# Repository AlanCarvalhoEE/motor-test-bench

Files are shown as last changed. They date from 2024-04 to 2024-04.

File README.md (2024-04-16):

# Motor Test Bench

This project consists of a test bench for small DC motors. The main objective of the system is to enable the characterization of motors with unknown data. The system performs measurements of rotational speed and torque of the motor under test while gradually varying the load on the motor shaft.

The speed is measured using a quadrature encoder. The encoder disc is coupled to the motor shaft and as it rotates, it generates pulses in an optical switch. Counting these pulses, when related to elapsed time, allows for the calculation of the rotational speed of the shaft.

The torque is indirectly measured. A lever arm is pressed against the motor shaft by a spring, whose tension can be varied, thereby altering the load on the shaft. The rotation of the motor shaft causes this lever arm to press against a load cell, which measures the applied force. By relating the measured force to the length of the lever arm, the torque is calculated.

During a test, the load on the motor shaft is gradually increased automatically. A stepper motor provides linear advancement under the spring, increasing its tension and consequently the load.

With the obtained data, it is possible to generate "torque vs. speed" and "power vs. speed" graphs of the motor, as well as identify parameters such as maximum speed, holding torque, and maximum power.

The current version of the project is still a prototype. In the next version, all electronics will be integrated, and new functionalities will be developed. The system will include measurement of the motor's input current, allowing for the calculation of its input power and consequently, its efficiency.

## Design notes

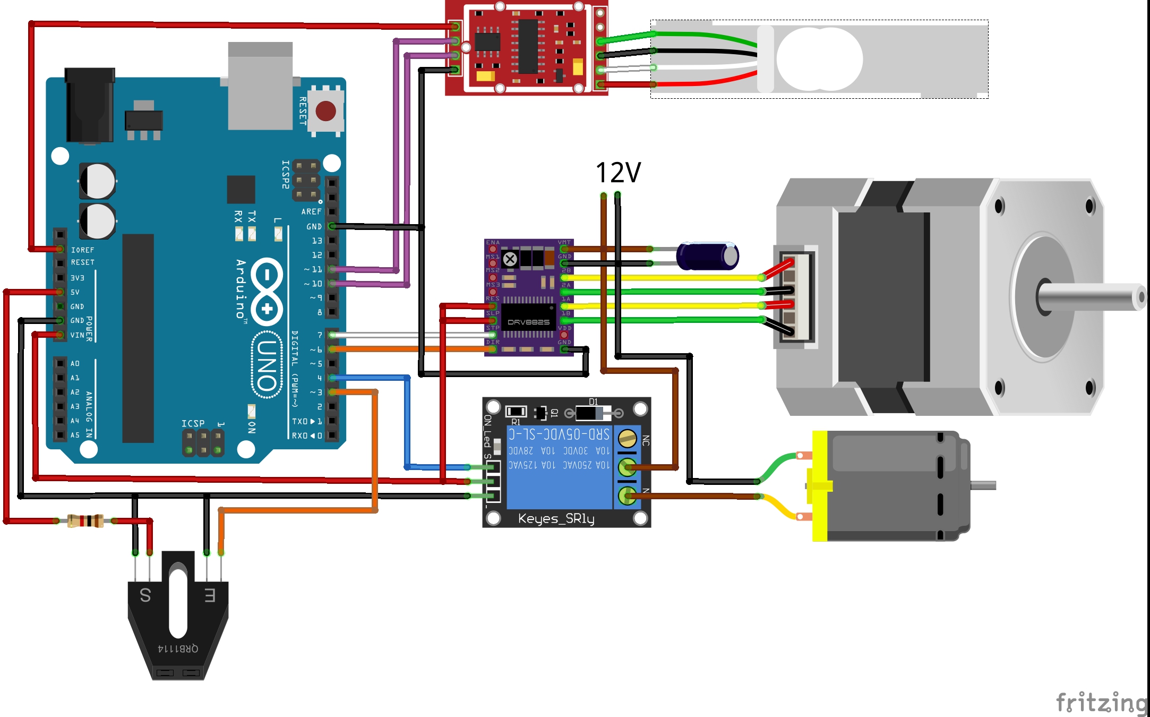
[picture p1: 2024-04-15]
Electronics/Electronics schematic.jpg

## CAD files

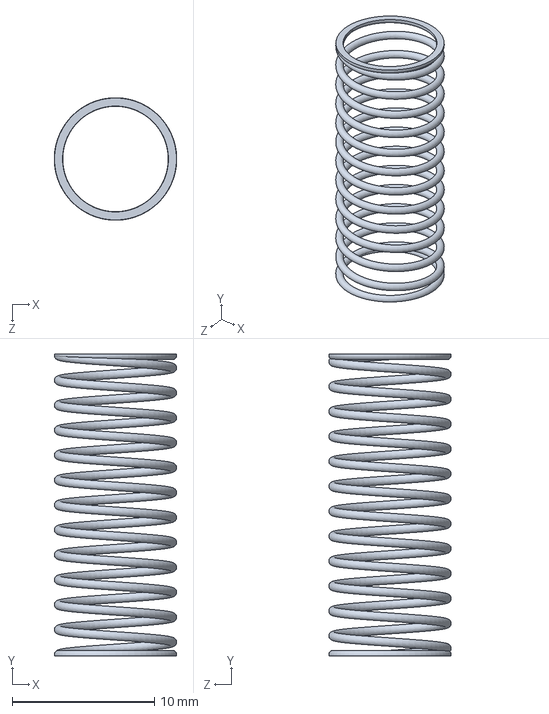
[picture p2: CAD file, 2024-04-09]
3D/Parts to buy/Spring 8x21.SLDPRT
8.60 x 21.2 x 8.60 mm

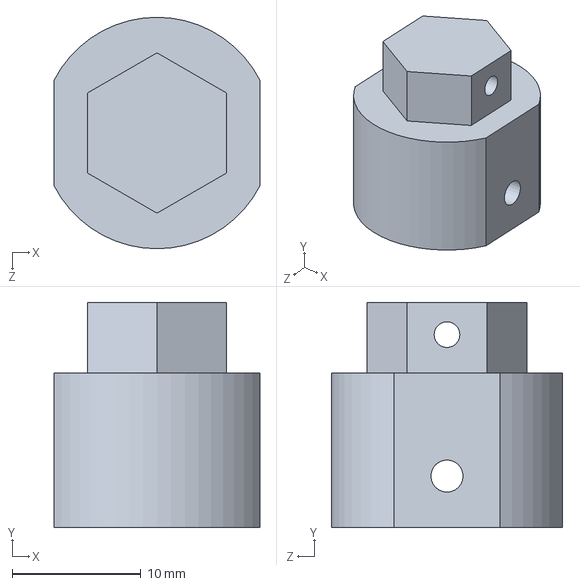
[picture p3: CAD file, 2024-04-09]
3D/Parts to manufacture/Stepper shaft adapter.SLDPRT
16.0 x 17.5 x 18.0 mm

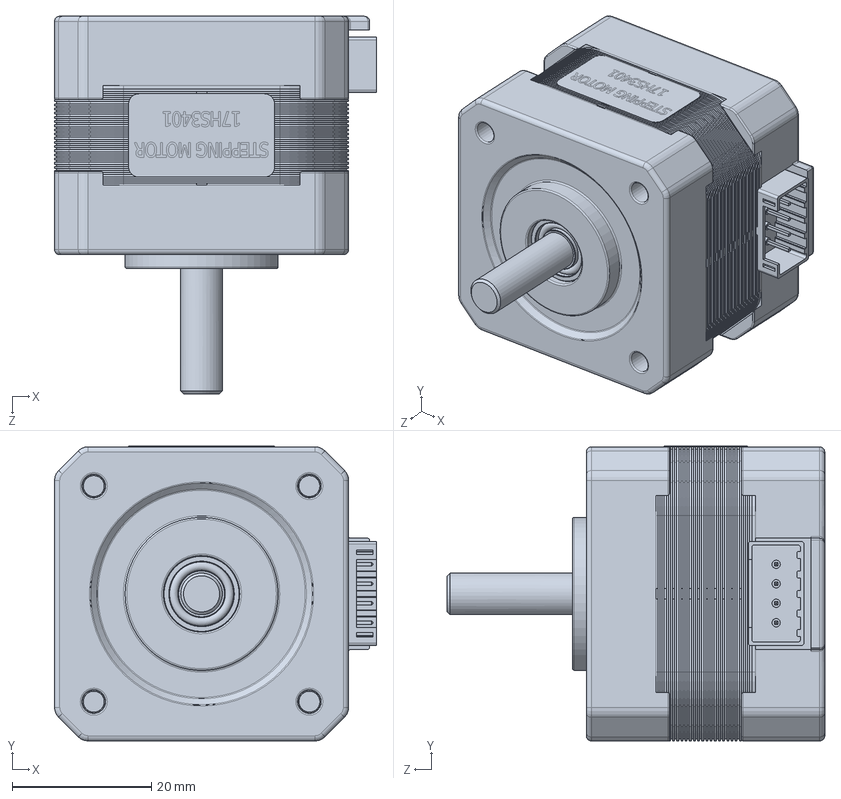
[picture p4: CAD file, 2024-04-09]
3D/Parts to buy/Stepper motor 17HS3401.SLDPRT
46.3 x 42.4 x 54.3 mm

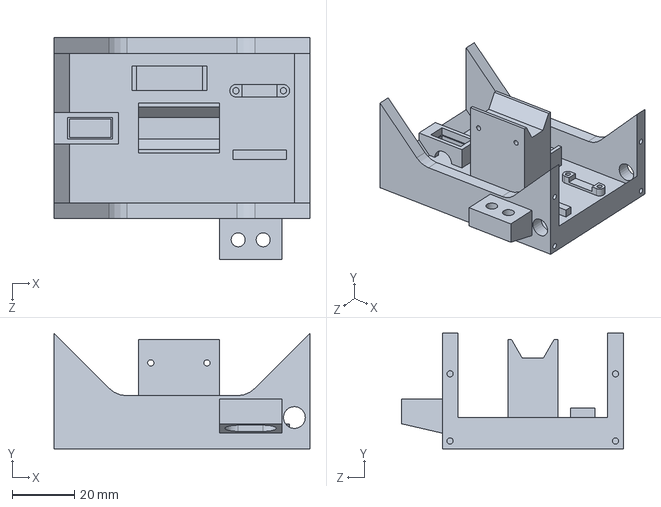
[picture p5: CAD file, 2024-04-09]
3D/Parts to manufacture/Base.SLDPRT
82.0 x 37.0 x 71.0 mm

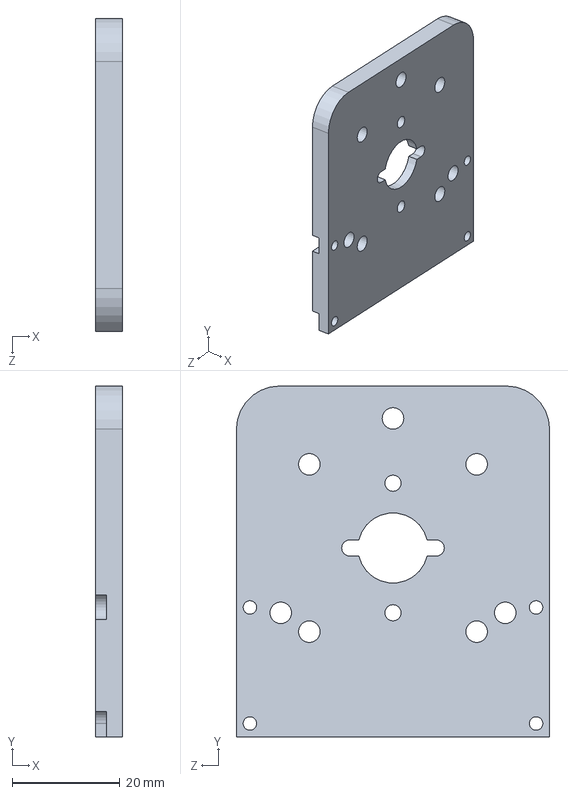
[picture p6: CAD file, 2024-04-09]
3D/Parts to manufacture/Test motor mount.SLDPRT
5.00 x 65.0 x 58.0 mm

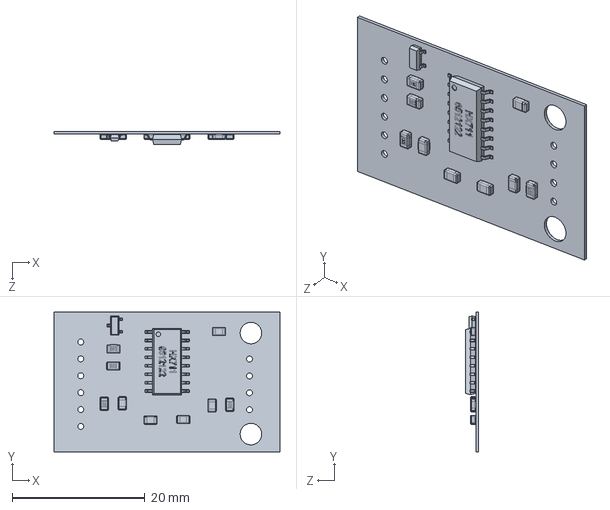
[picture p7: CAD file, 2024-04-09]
3D/Parts to buy/HX711 module.SLDPRT
34.0 x 21.0 x 1.97 mm

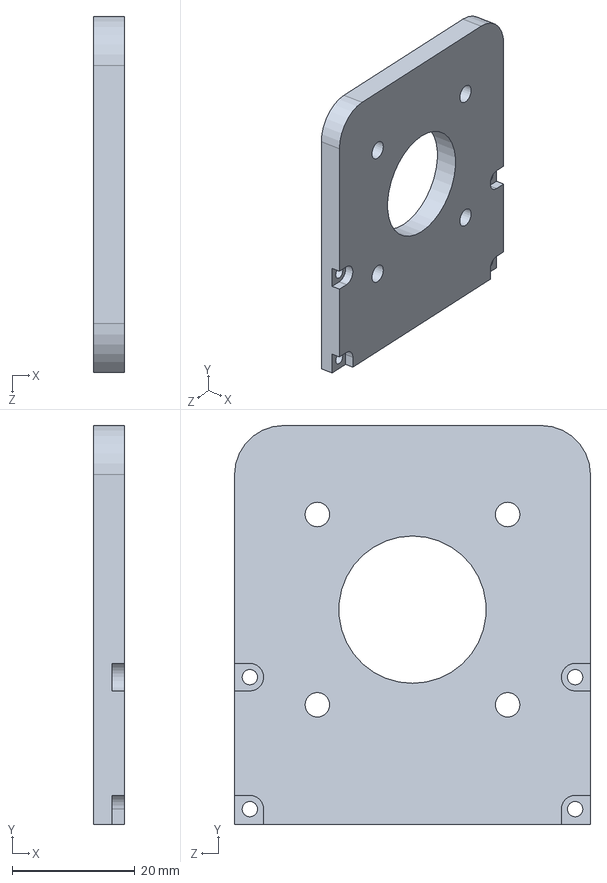
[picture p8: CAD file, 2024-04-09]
3D/Parts to manufacture/Stepper mount.SLDPRT
5.00 x 65.0 x 58.0 mm

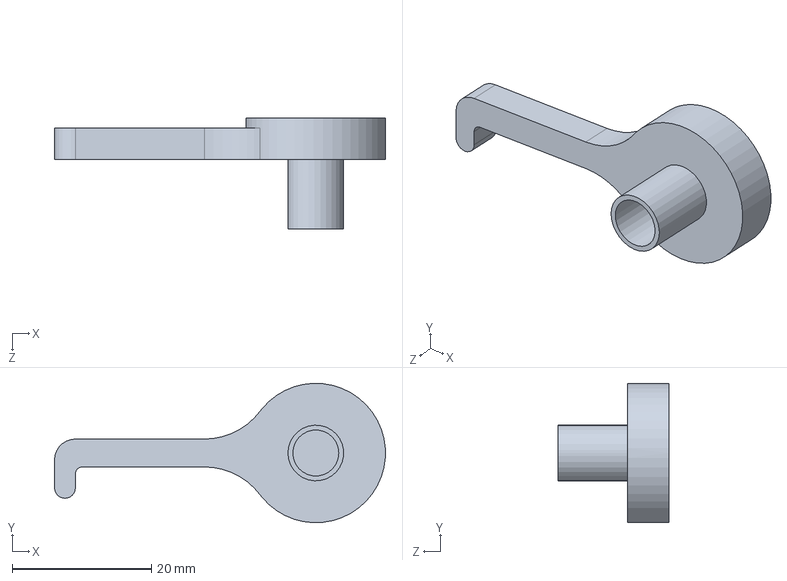
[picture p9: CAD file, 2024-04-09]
3D/Parts to manufacture/Lever arm.SLDPRT
47.5 x 20.0 x 16.0 mm

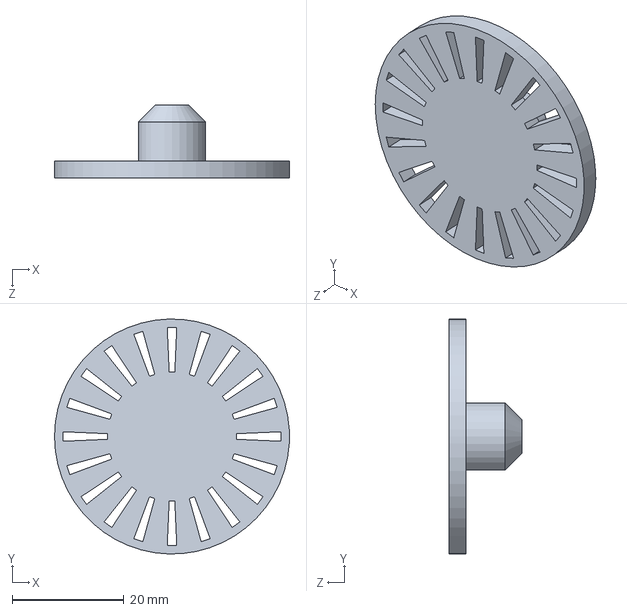
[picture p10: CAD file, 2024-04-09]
3D/Parts to manufacture/Encoder disk.SLDPRT
42.0 x 42.0 x 13.0 mm

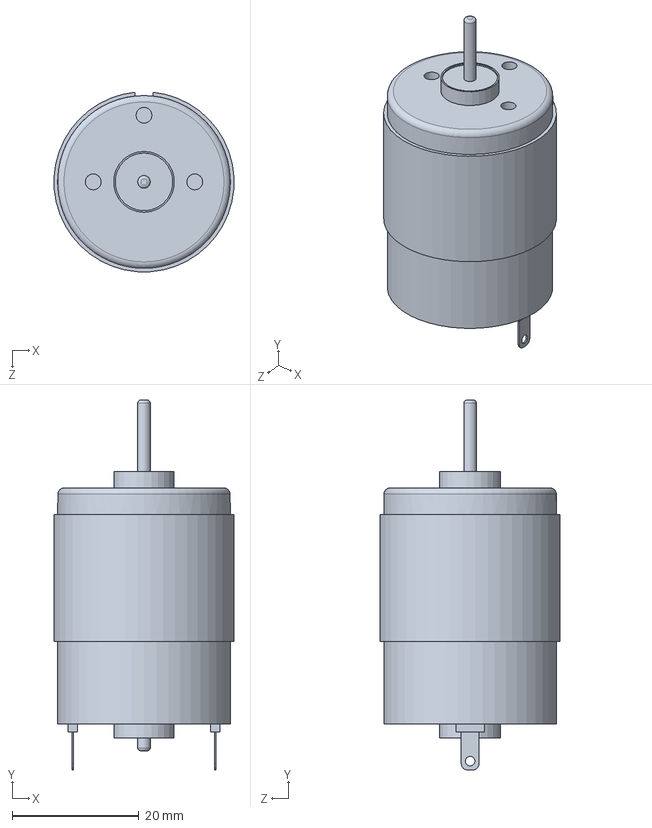
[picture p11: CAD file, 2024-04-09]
3D/Parts to buy/DC motor 27x37mm.SLDPRT
28.4 x 58.3 x 28.3 mm

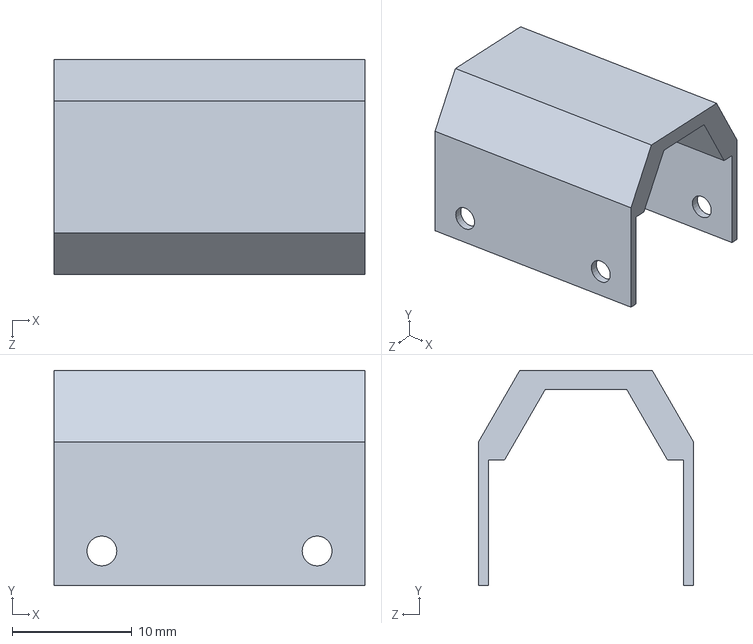
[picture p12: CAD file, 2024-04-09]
3D/Parts to manufacture/Spring cover.SLDPRT
26.0 x 18.0 x 18.0 mm

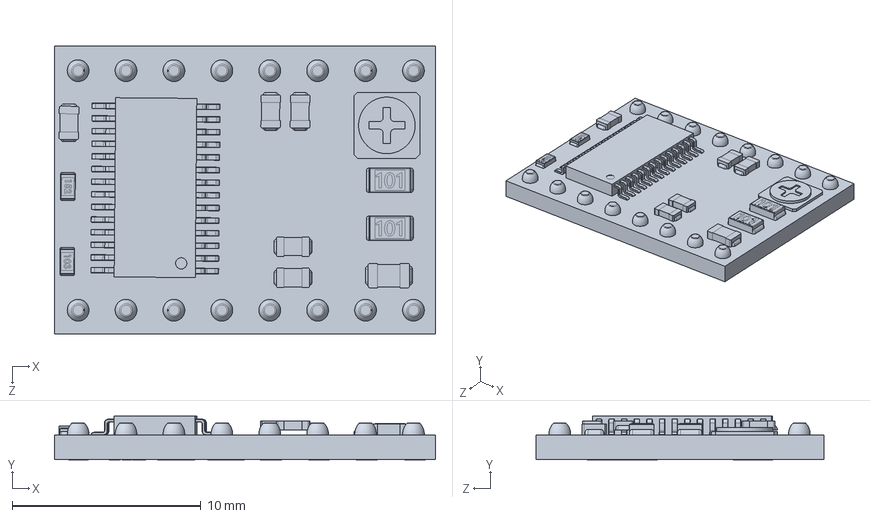
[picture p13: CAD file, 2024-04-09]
3D/Parts to buy/Stepper Motor Driver DRV8825.SLDPRT
20.2 x 2.31 x 15.2 mm

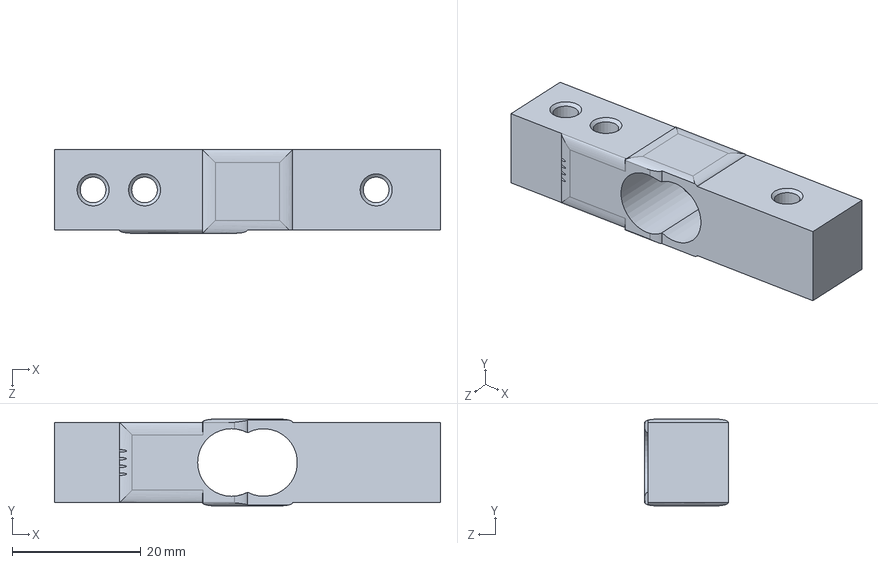
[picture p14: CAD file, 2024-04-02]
3D/Parts to buy/Load cell 5kg.SLDPRT
60.0 x 13.5 x 13.0 mm

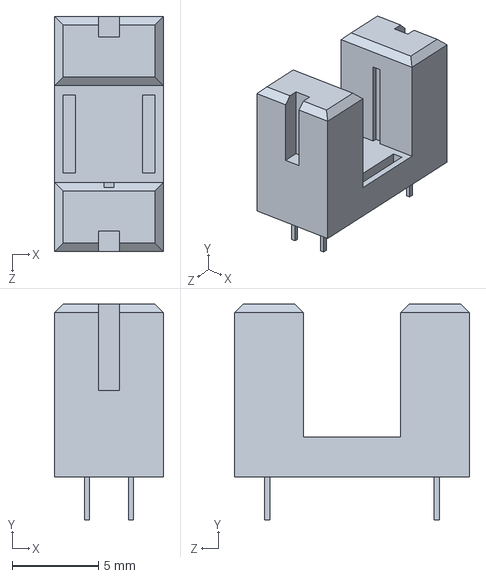
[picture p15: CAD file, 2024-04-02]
3D/Parts to buy/Optical Switch.SLDPRT
6.30 x 12.5 x 13.6 mm

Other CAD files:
3D/Bench assembly.SLDASM
3D/Parts to buy/Allen cilindrical head screw M4x10.SLDPRT
3D/Parts to buy/Hex screw M6x40.SLDPRT
3D/Parts to buy/Allen cilindrical head screw M3x8.SLDPRT
3D/Parts to buy/Allen button head screw M2,5x6.SLDPRT
3D/Parts to buy/Nut M6.SLDPRT
3D/Parts to buy/Phillips self-tapping pan head screw 2,2x6,5.SLDPRT
3D/Parts to manufacture/Screw adapter.SLDPRT

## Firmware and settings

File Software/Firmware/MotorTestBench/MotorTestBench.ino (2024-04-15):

// Motor Test Bench V1.0
// Developer: Alan Carvalho
// Date: 14/04/2024

#include "AccelStepper.h"  // Library to control the stepper motor
#include "HX711.h"         // Library to control the HX711 module

// HX711 pins
#define LOADCELL_DT 10
#define LOADCELL_SCK 11

// Relay pin
#define RELAY_S 4

// Optical switch pin
#define OPTICAL_SWITCH 3

// Stepper driver pins
#define STEPPER_DIR 6
#define STEPPER_STEP 7

// Bench parameters
#define STEPPER_SPEED -100    // Stepper motor speed
#define ARM_LENGTH 0.035      // Lever arm length (m)
#define ENCODER_POINTS 20.0   // Number of windows in the encoder disk
#define MAX_PULSES 100        // Number of pulses to restart the counting

HX711 loadCell;                                                       // HX711 library object
AccelStepper stepper = AccelStepper(1, STEPPER_STEP, STEPPER_DIR);    // AccelStepper library object

bool running = false;                   // Indicates the test is running
float mass = 0;                         // Mass on the load cell (g)
float torque = 0;                       // Torque generated by the motor (mN.m)
float speed = 0;                        // Motor shaft speed (RPM)
volatile int pulseCount = 0;            // Encoder pulse count
unsigned long currentTime = 0;          // Current time on speed calculation (ms)
unsigned long initialTime = 0;          // Initial time on speed calculation (ms)
const long readingInterval = 100;        // Interval between readings (ms)
unsigned long lastReading = 0;          // Time of the last reading (ms)
const long maximumPulseInterval = 1000; // Maximum time between two encoder pulse to assume it is not running (ms)
unsigned long lastPulseTime = 0;        // Time when the last encoder pulse happened (ms)
const long testFinishInterval = 3000;   // Interval to stop the test after the motor speed gets to zero (ms)
unsigned long zeroSpeedTime = 0;        // Time when the motor speed gets to zero (ms)


void setup() 
{
  Serial.begin(115200);  // Open the serial port

  // Configure pins
  pinMode(OPTICAL_SWITCH, INPUT_PULLUP);
  pinMode(RELAY_S, OUTPUT);

  // Configure the HX711 sensor
  loadCell.begin(LOADCELL_DT, LOADCELL_SCK);
  loadCell.set_scale(440);
  loadCell.tare();

  // Configure the interrupt to detect encoder pulses
  attachInterrupt(digitalPinToInterrupt(OPTICAL_SWITCH), countPulse, RISING);

  // Start with the motor turned off
  digitalWrite(RELAY_S, LOW);

  // Set stepper maximum speed
  stepper.setMaxSpeed(100);
}


void loop() 
{
  if (Serial.available() > 0) 
  {
    String command = Serial.readString();

    if (command.indexOf("START") > -1) startTest();
    else if (command.indexOf("STOP") > -1) stopTest(false);
  }

  if (running) 
  {
    stepper.runSpeed();

    if ((millis() - lastReading) > readingInterval) 
    {
      // Get all the necessary data
      getSpeed();
      getTorque();

      // Print the collected data on the serial port
      printData();

      lastReading = millis();
    }

    // Encoder is not moving
    if ((millis() - lastPulseTime) > maximumPulseInterval) pulseCount = 0;
  }
}


void getSpeed() 
{
  currentTime = millis() - initialTime;
  speed = 60000 * ((pulseCount / ENCODER_POINTS) / currentTime);
  if (speed < 0) speed = 0;

  if (pulseCount > MAX_PULSES) 
  {
    pulseCount = 0;
    initialTime = millis();
  }

  //if(speed == 0)
  //{
    //if(zeroSpeedTime == 0) zeroSpeedTime = millis();
    //else if ((millis() - zeroSpeedTime) > testFinishInterval) stopTest(true);
  //}
}

void getTorque() 
{
  mass = loadCell.get_units();
  torque = 9.81 * mass * ARM_LENGTH;
  if (torque < 0) torque = 0;
}

void countPulse() 
{
  pulseCount++;
  lastPulseTime = millis();
}

void printData() 
{
  Serial.print(speed);
  Serial.print("|");
  Serial.print(torque);
  Serial.println("");
}

void startTest()
{
  running = true;
  
  digitalWrite(RELAY_S, HIGH);
  
  Serial.println("MOTOR TEST STARTED");
  Serial.println("");
  Serial.println("Speed (RPM)|Torque (mN.m)");
     
  stepper.setSpeed(STEPPER_SPEED);
}

void stopTest(bool status)
{
  running = false;
  pulseCount = 0;
  zeroSpeedTime = 0;
  
  digitalWrite(RELAY_S, LOW);
  
  if (status) Serial.println("MOTOR TEST FINISHED");
  else Serial.println("MOTOR TEST STOPPED");
  Serial.println("");

  stepper.stop();
}

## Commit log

2024-04-01 3D models included
    [Current sensor module ACS712.SLDPRT, Encoder disk.SLDPRT, Encoder disk.STL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]
2024-04-02 3D models updated
    [Allen button head screw M2,5x6.SLDPRT, Allen cilindrical head screw M3x10.SLDPRT, Current sensor module ACS712.SLDPRT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]
2024-04-03 Friction brake improved
    [Adjustment nut mount.SLDPRT, Adjustment nut mount.STL, Allen cilindrical head screw M3x10.SLDPRT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]
2024-04-04 Electronics schematic done
    [Motor test bench.fzz]
2024-04-04 Schematic updated
    [Motor test bench.fzz]
2024-04-05 Brake system improved
    [Allen cilindrical head screw M4x20.SLDPRT, Bench assembly.SLDASM, Nut M4.SLDPRT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]
2024-04-05 Firmware updated for the new brake system
2024-04-05 Schematics updated
    [Motor test bench.fzz]
2024-04-07 Stepper control implemented
2024-04-07 New assembly finished
    [Adjustment nut mount.SLDPRT, Adjustment nut mount.STL, Allen cilindrical head screw M3x25.SLDPRT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]
2024-04-09 Base divided in 3 parts
    [Base.SLDPRT, DC motor 27x37mm.SLDPRT, HX711 module.SLDPRT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]
2024-04-10 Improved stepper control
2024-04-15 Prototype code finished
2024-04-15 Prototype schematic finished
    [Motor test bench.fzz]
